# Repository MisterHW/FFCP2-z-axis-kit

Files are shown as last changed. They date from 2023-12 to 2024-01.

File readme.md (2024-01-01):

# z-axis lead screw replacement for Creator Pro 2 

Components:
- 1x Hanpose 17HS3401S-T8*8-300 stepper motor (NEMA17 size, 4-start Tr8x8 lead screw, 300 mm length (up to 310 mm)
- 1x 608Z bearing
- 1x **printed** end support block for 10 mm chrome steel rails, including
- 4x M3x4 heat-set inerts
- replacement for StepDrv v2.1 motor drivers or current adjustment (right after replacing, the current is too low)

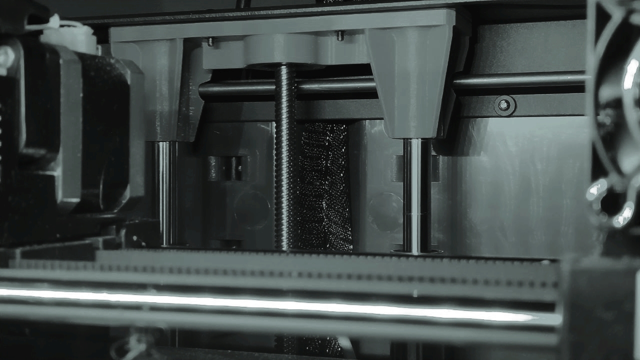
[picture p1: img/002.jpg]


## Lead Screw Replacement

Due to layer height inconsistencies and perceptible jamming every full turn, the lead screw of this FlashForge Creator Pro 2 was replaced. The total print time amounted to 266 hours at this point.

Unfortunately, the stock part (Bohong Stepping Motor 42HB34F04ASG-38) is reduced to a 5 mm (-30µm) section with 20 mm length to insert into a thin section bearing pressed into the original plastic end support, the fit of which was found to be loose. 

Top: old unit, bottom: replacement part.

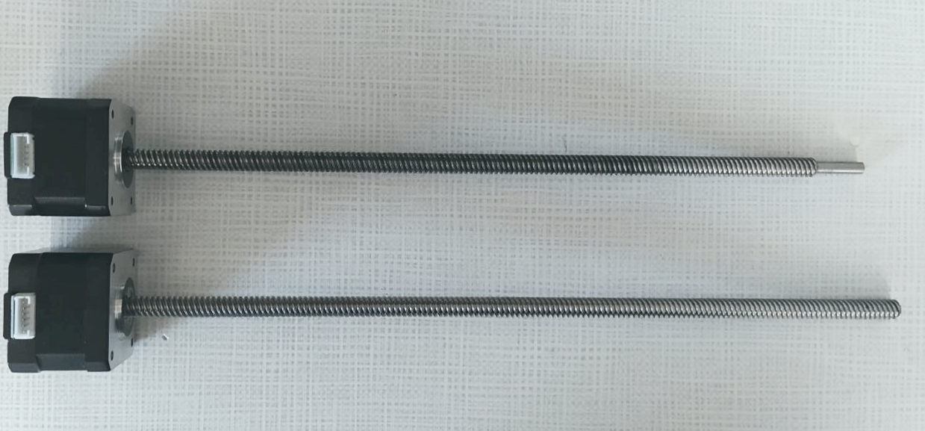
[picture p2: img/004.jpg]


## Old Support Block

After removing the bottom cover, unplugging the stepper motor and removal of the 8 screws holding top and bottom supports in the printer frame, the z axis assembly and print bed can be pulled out of the printer frame, starting by pulling the top support towards the inside of the printer.

When measuring, distances of the rails were found to be 99.92 mm at the bottom and 99.65 mm at the top. hinting at a possible cause for the screws of the linear bearings to have worked themselves loose.

The injection moulded parts are not visually impressive, but they primarily need to resist horizontal movement. Sink marks around the rod mounts are visible. The shafts were removed by holding in an ER32 collet block and a twisting motion.

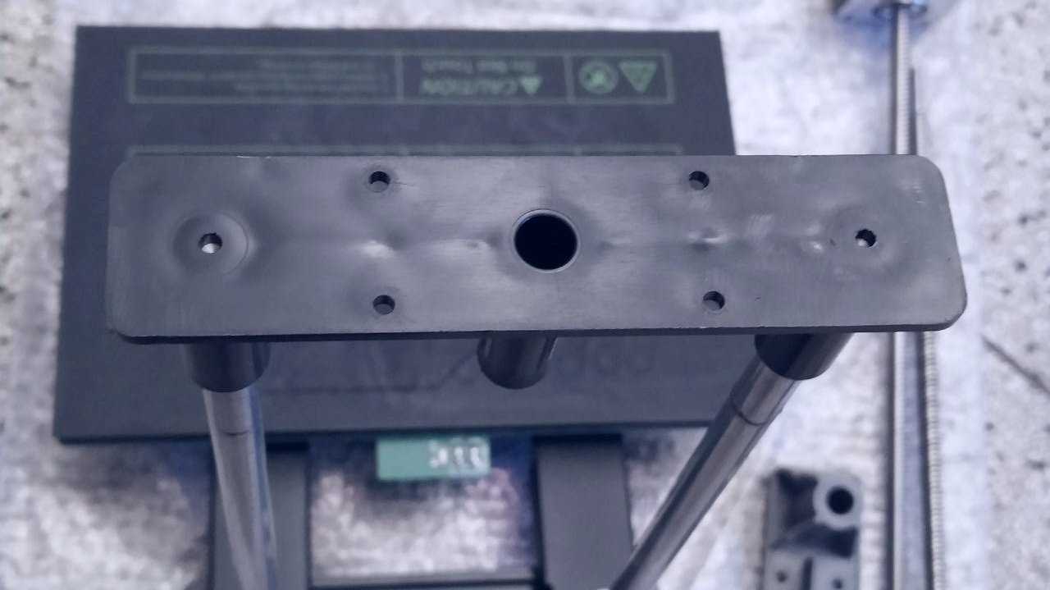
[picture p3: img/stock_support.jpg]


## New Support Block

The design files are provided in this repository. For best results, clean up the holes with a 10mm F7 reamer, insert the original chrome steel shafts, zero calipers on the OD of one shaft, then measure the outsides of the pair of shafts as they're in place. To validate the model, the part was printed in PLA and came out measuring 99.96 mm. Keepin mind that to avoid deformation in warm operating conditions, a more temperature resistant filament type should be considered.

For the insertion of the 608 bearing, a tool should be used that presses down on the outer race.

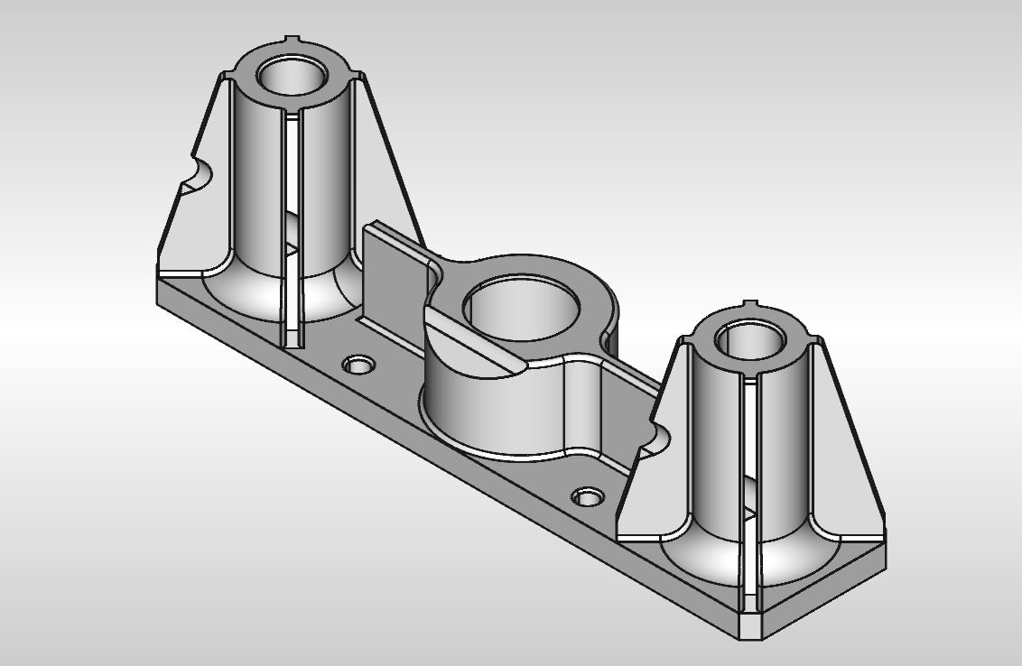
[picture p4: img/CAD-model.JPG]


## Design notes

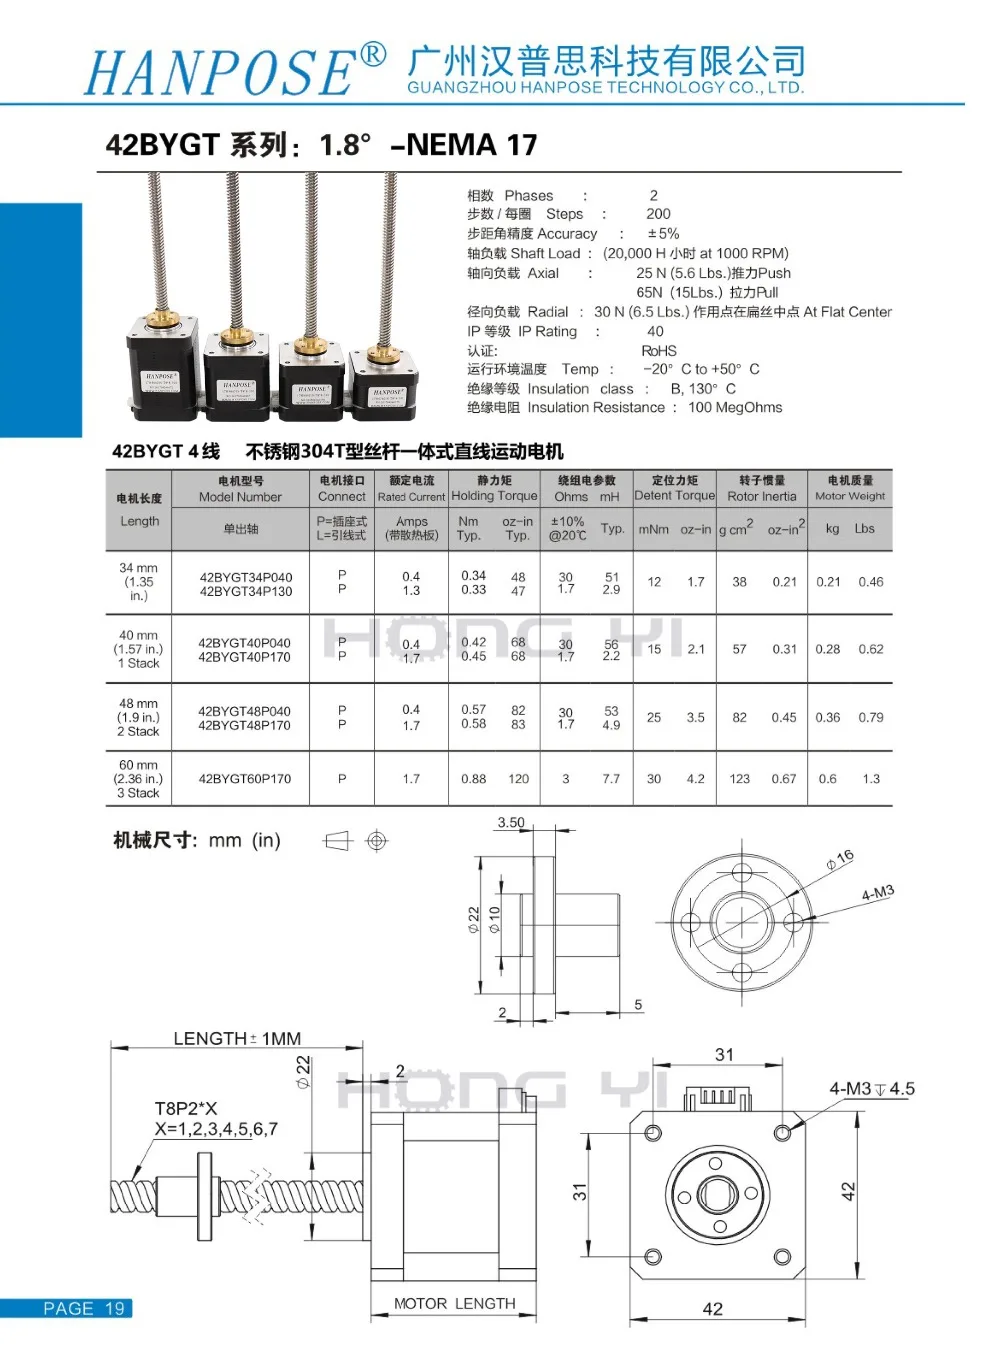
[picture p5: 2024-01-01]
img/17hs3401s-t8-8mm-nema17.webp

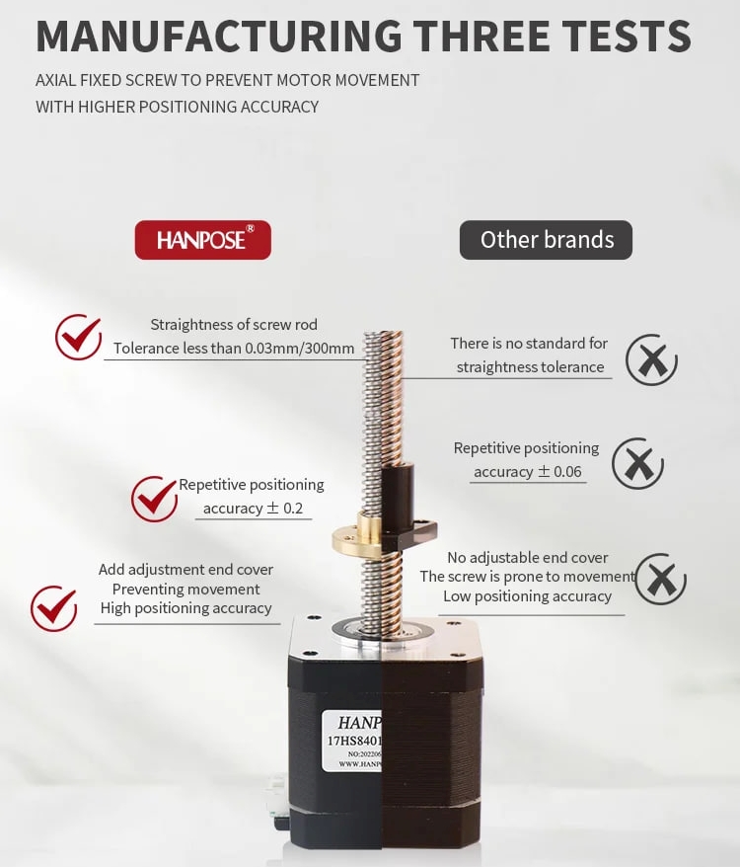
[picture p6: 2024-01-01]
img/Hanpose_stepper.jpg

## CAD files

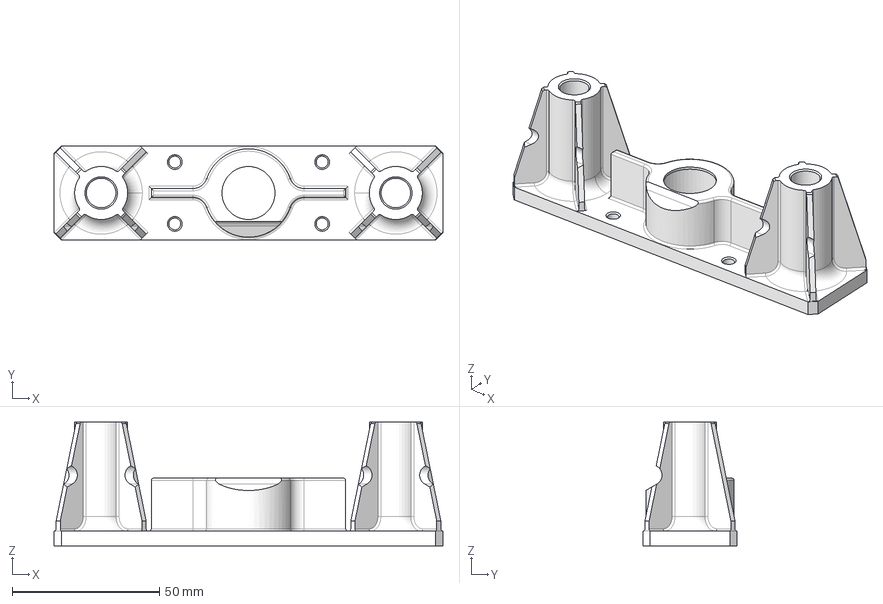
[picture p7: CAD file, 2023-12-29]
FF_CreatorPro2_vertical-support.step
132.0 x 32.0 x 42.0 mm

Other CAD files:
FF_CreatorPro2_vertical-support.3mf
FF_CreatorPro2_vertical-support.FCStd

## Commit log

2023-12-29 add z-axis top support block design
    [FF_CreatorPro2_vertical-support.FCStd]
2023-12-29 add export for 3D printing
    [FF_CreatorPro2_vertical-support.3mf, FF_CreatorPro2_vertical-support.step]
2024-01-01 add hint about motor current
    the original StepDrv v2.1 (A4988) driver for the z axis should be adjusted towards a higher motor current (higher setpoint voltage) or replaced with TMC2208.
